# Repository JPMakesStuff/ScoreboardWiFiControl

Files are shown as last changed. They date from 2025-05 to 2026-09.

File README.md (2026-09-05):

# ScoreboardWiFiControl
Replacement for Varsity/All-Star/BSN/Sportable Baseball scoreboard controllers

Manufacturer's ancient and expensive remote was either a 5pin DIN connector that seemed to be RS-485 (but maybe not quite) or included the artaflex 2.4Ghz module (EOL 2018) which constantly disconnected; possibly because of a poorly designed heartbeat signal that can't ever be missed, or because it conflicted with every other 2.4Ghz WiFi network around. This remote drained batteries at an astounding rate; due to a design flaw where the power switch doesn't actually disconnect the battery.

Solution: Replace the manufacturer's control box with an [Arduino UNO R4 WiFi board](https://www.amazon.com/dp/B0C8V88Z9D), but keep the manufacturer dual output 35v/12v power supply that runs the LEDs.

Now anybody can use a **WiFi connected phone/tablet/laptop to control the scoreboard!**

Security should be accomplished by a dedicated wireless SSID just for the scoreboard(s) and for your coaches/announcers/trusted family member to connect.

Example webpage... (Make it an "app" icon using browser options menu, "Add to Home screen")<br/>
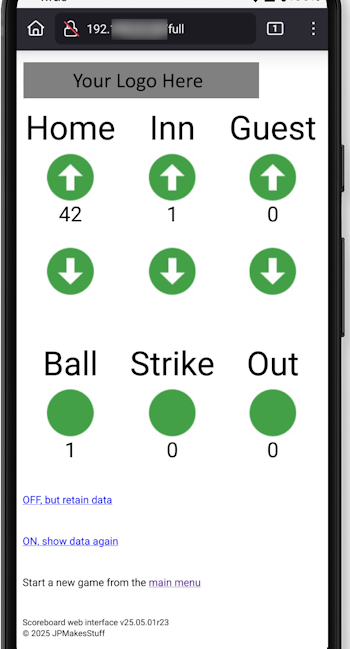
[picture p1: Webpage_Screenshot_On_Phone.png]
Webpage_Screenshot_On_Phone


## Software for Arduino

For the [3314](https://github.com/JPMakesStuff/ScoreboardWiFiControl/blob/main/3314.jpg) baseball scoreboard<br/>
...use the Arduino code "[ard_scoreboard](https://github.com/JPMakesStuff/ScoreboardWiFiControl/tree/main/ard_scoreboard)"

For the [3320](https://github.com/JPMakesStuff/ScoreboardWiFiControl/blob/main/3320.jpg) baseball scoreboard<br/>
...use the Arduino code "[ard_bigscoreboard](https://github.com/JPMakesStuff/ScoreboardWiFiControl/tree/main/ard_bigscoreboard)"

Graphics are a sprites file so there's only a single .png request (prevents upsetting Arduino's little web server as opposed to 10+ image requests)  If you want to insert your own logo and touch button graphics you could edit the [example .png graphic](https://github.com/JPMakesStuff/ScoreboardWiFiControl/blob/main/sprites_example.png), keeping the same placement and dimensions, then ask ChatGPT to create the arduino_images.h file from your .png file.

Your WiFi details need to be added in the arduino_secrets.h file.

To upload the sketch to your Arduino you need...
 - [Arduino IDE](https://www.arduino.cc/en/software/) (v2.3.8 as of today)
 - Install all the USB drivers when prompted
 - Tools > Board > Boards manager ... search "R4" ... Arduino UNO R4 Boards ... Install (v1.5.3 as of today)
 - Tools > Manage libraries ... search "graphics" ... ArduinoGraphics ... Install (v1.1.5 as of today)
 - Tools > Board > Arduino UNO R4 Boards > pick Arduino UNO R4
 - Tools > Port > pick COM # (the correct COM port number will be the one that shows up after plugging the Arduino into your computer)
 - Sketch > Upload

After applying power the Arduino's LED matrix briefly scrolls the last two octets of the IP address it got assigned. For example if your network DHCP server hands out 192.168.1.8 to the Arduino, the display would scroll 1.8
If this never happens then either your WiFi details are incorrect, out of range, you have some other network problem, or the Arduino is never fully booting.

## Hardware connections

The ribbon cable must be unplugged from the manufacturer's control box<br/>
(usually located behind the large hatch below or behind the inning digit)<br/>
Example pinout...<br/>
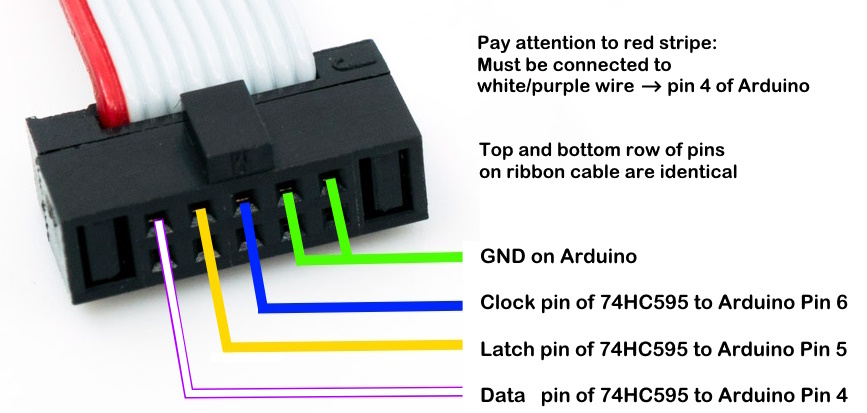
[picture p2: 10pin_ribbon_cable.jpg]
10pin connector


On the [cable I sell](https://jpelectron.etsy.com) pay attention to the colors plugged into the Arduino...<br/>
 - GND on Arduino is $\color{Green}{\textsf{Green}}$ wire</br>
 - Pin 6 on Arduino is $\color{Blue}{\textsf{Blue}}$ wire<br/>
 - Pin 5 on Arduino is $\color{Yellow}{\textsf{Yellow}}$ wire<br/>
 - Pin 4 on Arduino is White or $\color{Purple}{\textsf{Purple}}$ wire<br/>
...see the [picture here](https://github.com/JPMakesStuff/ScoreboardWiFiControl/blob/main/Example_Arduino_Connection.jpg) of Arduino connection</br>

Valid ways of connecting to the ribbon cable without butchering it are...<br/>
 - [cable I sell](https://jpelectron.etsy.com)
 - [Dual Rows 2.54mm 0.1" Pitch Shrouded IDC Male Header](https://www.amazon.com/dp/B00B3PI02G)
 - [Male IDC Socket 10 Pin 2x5 Pin 2.54mm Pitch](https://www.amazon.com/dp/B08T1YDG8M)

I spent days reverse engineering this, drop me a line if it helped you, or if you've adapted it to another model scoreboard!  If you'd like assistance in repair of your scoreboard or implementation of this new WiFi control method please contact me.  As of today I sell the [Arduino interface cable](https://www.etsy.com/listing/4490992543/arduino-to-baseball-scoreboard-control) on my Etsy shop and hope to offer full hardware conversion kits in the future if the demand is there.

## WiFi technical info

In my implementation we are using the following hardware...
 - TP-Link Omada firewall ER605v2 https://www.amazon.com/dp/B08QTXNWZ1<br/>
   ...also allows for content filtering to keep limited wireless bandwidth available for the GameChanger app
      (such as no YouTube, Hulu, Disney+ or adult sites)
 - TP-Link Omada wireless controller OC220 https://www.amazon.com/dp/B0FRW8GM11<br/>
   ...this is required to put the scoreboard mounted APs into mesh mode
 - TP-Link EAP610 Outdoor AP https://www.amazon.com/dp/B0B231J81C<br/>
   ...one goes on the concessions building, one goes on the scoreboard
 - Universal Wireless mount 2pk https://www.amazon.com/dp/B0BCNZFNTD<br/>
   ...makes it easy to mount the APs so they face each other
 - RasPi 4 model B with 4GB RAM https://www.amazon.com/dp/B07TD42S27<br/>
   ...this acts as a [Tailscale subnet router](https://tailscale.com/docs/features/subnet-routers) so I can control the scoreboards from anywhere, even when I'm home and not on the field WiFi

I intentionally decided to use an Arduino with WiFi as opposed to an Arduino with Ethernet; since each scoreboard has it's own AP mounted on it the signal is great and some level of lightning protection is achieved by not having a direct Ethernet connection to the AP.

As currently implemented both the Arduino and your end-users should connect to the same wireless SSID, the Arduino should be given a DHCP reservation (so the IP doesn't change) on the network, and optionally a DNS A record pointing to that IP for an easy to remember name.  Arduino code could be modified so the Arduino broadcasts it's own SSID (AP mode) but this is considerably less reliable in terms of WiFi channel saturation and end-user connection simplicity, so I strongly suggest against this. If the wireless doesn't actually provide Internet, users will have to pick "stay connected" on their device, some devices don't handle this well and won't continue to route Internet out the cellular connection resulting in loss of calls, text messages, or other app data.

## More technical info

Scoreboard digits are connected internally by a 10pin ribbon cable, of which only 4 pins are useful (doubled up for redundancy against broken lines, I guess?) This cable connects to a HC595 IC (8-Bit Shift Register), which turns "on" a channel of the ULN2803A (NPN Darlington Transistor Array) which allows 35v power to flow through a voltage regulator to 2 sets of 13 LEDs in series, which makes up a segment of the digit, or a dot.

On the [3314](https://github.com/JPMakesStuff/ScoreboardWiFiControl/blob/main/3314.jpg) baseball scoreboard this cable is routed like this...<br/>
Arduino --> Left home digit (10's) --> right home digit (1's) --> Inning --> Dot driver board --> Left guest digit --> Right guest digit<br/>
...remove the ribbon cable from control box found on the front side, hatch below the inning digit<br/>
See [3314 wiring diagram](https://github.com/JPMakesStuff/ScoreboardWiFiControl/blob/main/LED_repair_info/3314-Wiring-Diagram.png)

On the [3320](https://github.com/JPMakesStuff/ScoreboardWiFiControl/blob/main/3320.jpg) baseball scoreboard they routed this cable in what I suppose was efficient for saving on copper wire but full on silly for programming...<br/>
Arduino --> BallDigit, Inn1guest, Inn1home, Inn2home, Inn2guest, Inn3guest, Inn3home, Inn4home, Inn4guest, Inn5guest, Inn5home, Inn6home, Inn6guest, StrikeDigit, Inn7guest, Inn7home, Inn8home, Inn8guest, Inn9guest, Inn9home, LeftHomeDigit, RightHomeDigit, RightGuestDigit, LeftGuestDigit, OutDigit<br/>
...remove the ribbon cable from control box found on the front side, hatch above the 2nd inning guest score digit

Do NOT connect the ribbon cable to both your Arduino and the manufacture's control box at the same time, doing so will impede the signal to control any of the digits.

Arduino power should NOT be sourced from the custom 12v/35v power supply within the manufacture's control box as it doesn't seem to supply enough amperage for another load on the 12v rail, you will find that the Arduino randomly resets if many digits are 8 (all segments lit up)

I power the Arduino using a [5v 2amp USB power supply](https://www.amazon.com/dp/B07DCR29GN) feeding into either the USB-C port or the 5v pin on the Arduino.  Optionally you could also use a 7.5v or 9v power supply feeding into the barrel jack, realizing this is dropped down to 5v via Arduino's on-board voltage regulator.

120VAC can be obtained from the small hatch on the back of the scoreboard near the power entry point, or by using an [IEC splitter](https://www.amazon.com/dp/B0BGPXDYSM) before it goes into the manufacture's control box.

Note on the manufacture's power supply located inside the control box...<br/>
MeanWell PD85-SP with dual output 12VDC 0.25A + 35VDC 2.3A (which I can't find anywhere today, perhaps was custom built just for Varsity)<br/>
Someday this will die and I expect having to source a more common 36v supply and using the internal trim pot found on most MeanWell supply's to make it output 35v, having a separate 12v power supply, then connecting both GNDs together.<br/>
 - Red wire is 35v rail - used to power the LED segments via several voltage regulators, one for each segment of the 7-segment digit<br/>
 - Brown wire is 12v rail - used to power a single voltage regulator on each digit which drops to 5v to power the HC595 and ULN2803A chips<br/>
 - Black wire is GND<br/>

In my case the scoreboards were all outdoors and all seemed to be getting wet inside, plus the fact that it's a big metal box means putting the Arduino inside the scoreboard isn't the best for WiFi connectivity, so I elected to move the power supply and control circuitry to a [weatherproof box](https://www.amazon.com/dp/B0BFPXDN8M) and split the 120VAC using [this terminal block](https://www.amazon.com/dp/B0DNJRQP32).  Each scoreboard has a wireless AP in a mesh configuration that connects them all back to the source of the WiFi at the concessions building.

See [example of my new control box](https://github.com/JPMakesStuff/ScoreboardWiFiControl/blob/main/Example_control_box.jpg)

## LED digit or dot testing aid

To test individual digit boards, or the "vane driver" board for (ball/strike/out) dots<br/>
Arduino --> 10pin ribbon cable --> only one digit at a time, not the entire scoreboard!<br/>
 - no other digits should be daisy-chained via additional ribbon cables connected to "output"<br/>
 - it's OK to keep the 3pin power cable connected to all, unless your trying to isolate a damaged/corroded/shorted digit or dot<br/>
 - **you MUST connect all GND together: the Arduino GND to the ribbon cable GND is then connected to the power supply GND via the digit**<br/>
 - use the Arduino code "[LED_tester](https://github.com/JPMakesStuff/ScoreboardWiFiControl/tree/main/LED_tester)"<br/>
 - modify the SSID section near the top to match your WiFi on the field, or your home WiFi, or your phone's hotspot when testing anywhere

See [example of test page](https://github.com/JPMakesStuff/ScoreboardWiFiControl/blob/main/Webpage_Screenshot_LED_tester.png)

## LED repair info

Digit<br/>
PCB - 1600129<br/>
PCA - 1500129<br/>
REV C<br/>

Dots<br/>
PCB - 1600131<br/>
PCA - 1500131<br/>
REV A<br/>

35v in → LM317 + 30 Ω → ~42 mA constant current → two parallel strings of 13 × 1.8v LEDs (voltage of drop ~23.4v) → ~20–21 mA per LED

LED size = T-1 3/4 5mm = DigiKey part 350-5218765F-ND, Mfg part 5218765F by Dialight

https://varsityscoreboards.com/scoreboard-parts/led-dots/replacement-2-inch-outdoor-dot/

https://varsityscoreboards.com/uncategorized/vane-dot-driver-board-1500055

https://varsityscoreboards.com/uncategorized/outdoor-15-led-digit-panel-1501015-12

See [LED repair info](https://github.com/JPMakesStuff/ScoreboardWiFiControl/blob/main/LED_repair_info)

## Notes for cost comparison

~$263 for my control box (including conformal coating the PCBs, caulk, weatherproof box, screws, Arduino, 5v power supply, and wireless AP)

https://scoreboard-parts.com/1006647-Semtech-Sportable-Varsity-Scoreboard-Driver-101MOD2.html
$975 | SKU# 1006647-Semtech

https://scoreboard-parts.com/1006649-SEMTECH-Sportable-Varsity-Wireless-Controller.html
$950 | SKU# 1006649-SEMTECH

https://scoreboard-parts.com/101MOD2-Sportable-Varsity-Scoreboard-Driver.html
$1,562.95 | SKU# 101MOD2

https://scoreboard-parts.com/1001LCDW-Sportable-Varsity-Wireless-Controller.HTML
$1,824.95 | SKU# 1001LCDW

...I'm not paying that for something that disconnects and resets the score 95% of the time.

[How it's made YouTube video](https://www.youtube.com/watch?v=2Ui810LpJfk) showing scoreboard assembly process

[Outdoor installation video](https://www.youtube.com/watch?v=sqrrQPMJL8o) by the same company

[End of Line]

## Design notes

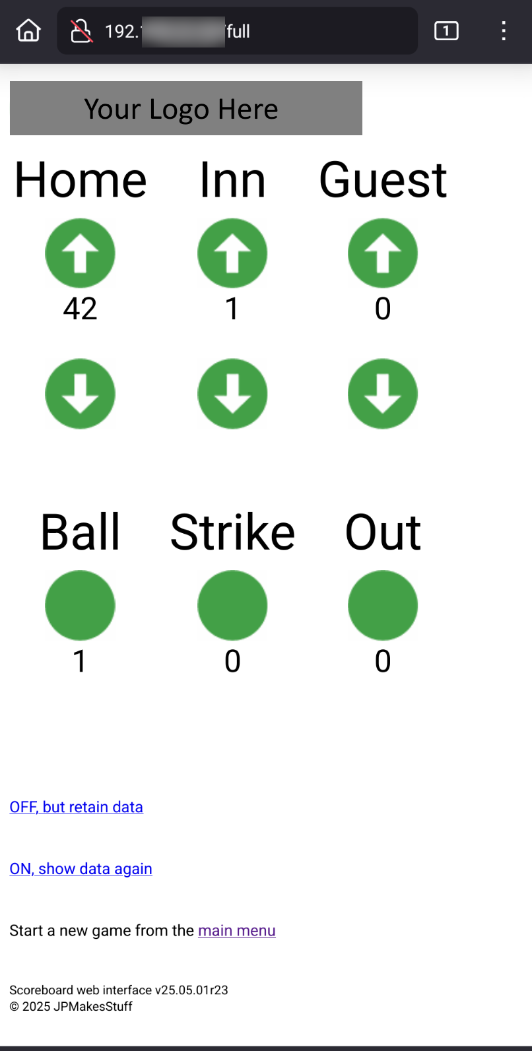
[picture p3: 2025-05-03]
Webpage_Screenshot.png

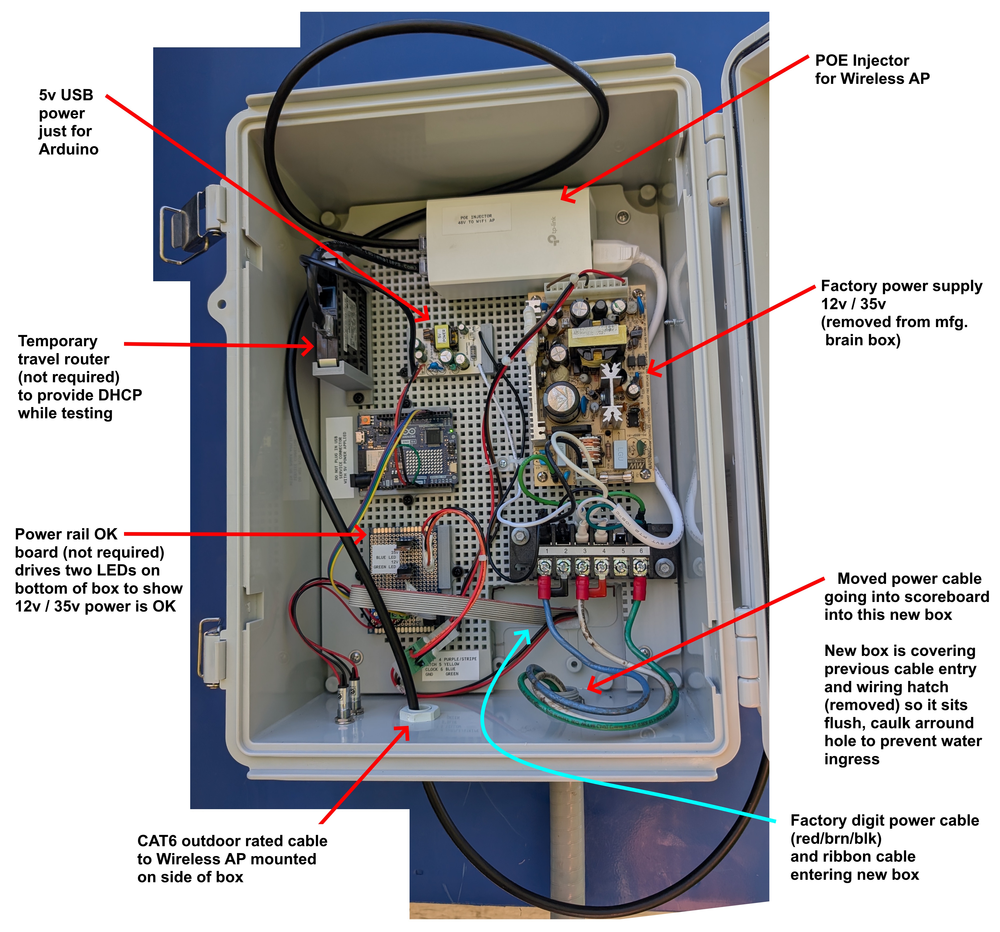
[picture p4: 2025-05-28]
Example_control_box.jpg

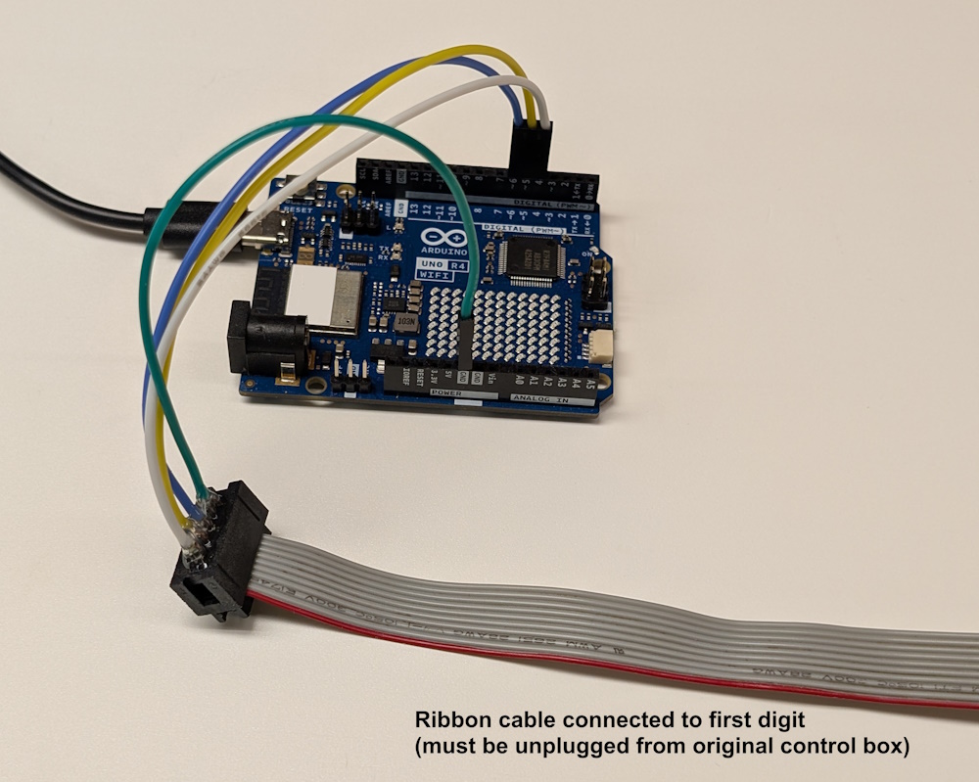
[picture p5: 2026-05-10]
Example_Arduino_Connection.jpg

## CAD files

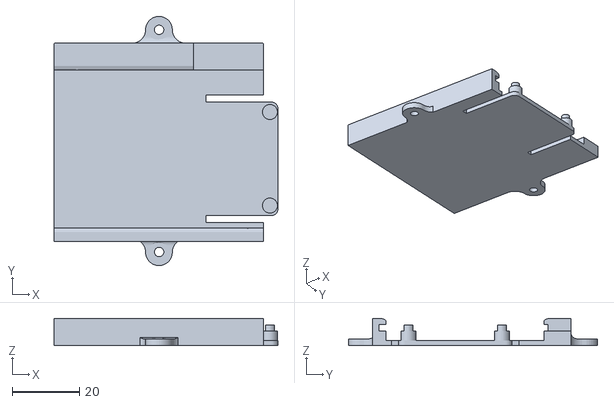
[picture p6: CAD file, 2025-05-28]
3D_print_files/Baseball SB Connections vReg PCB mount.stl
66.8 x 74.3 x 8.10

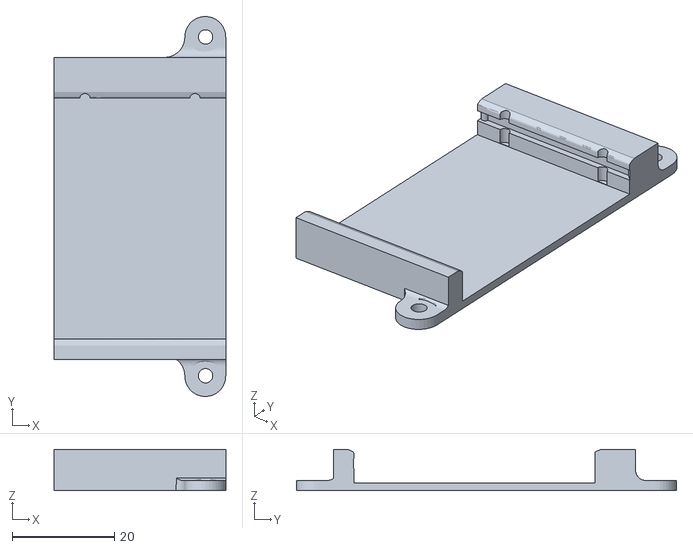
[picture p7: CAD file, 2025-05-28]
3D_print_files/Baseball SB 5v 2a PS mount.stl
33.6 x 74.3 x 8.10

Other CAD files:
3D_print_files/Baseball SB Arduino mount.stl

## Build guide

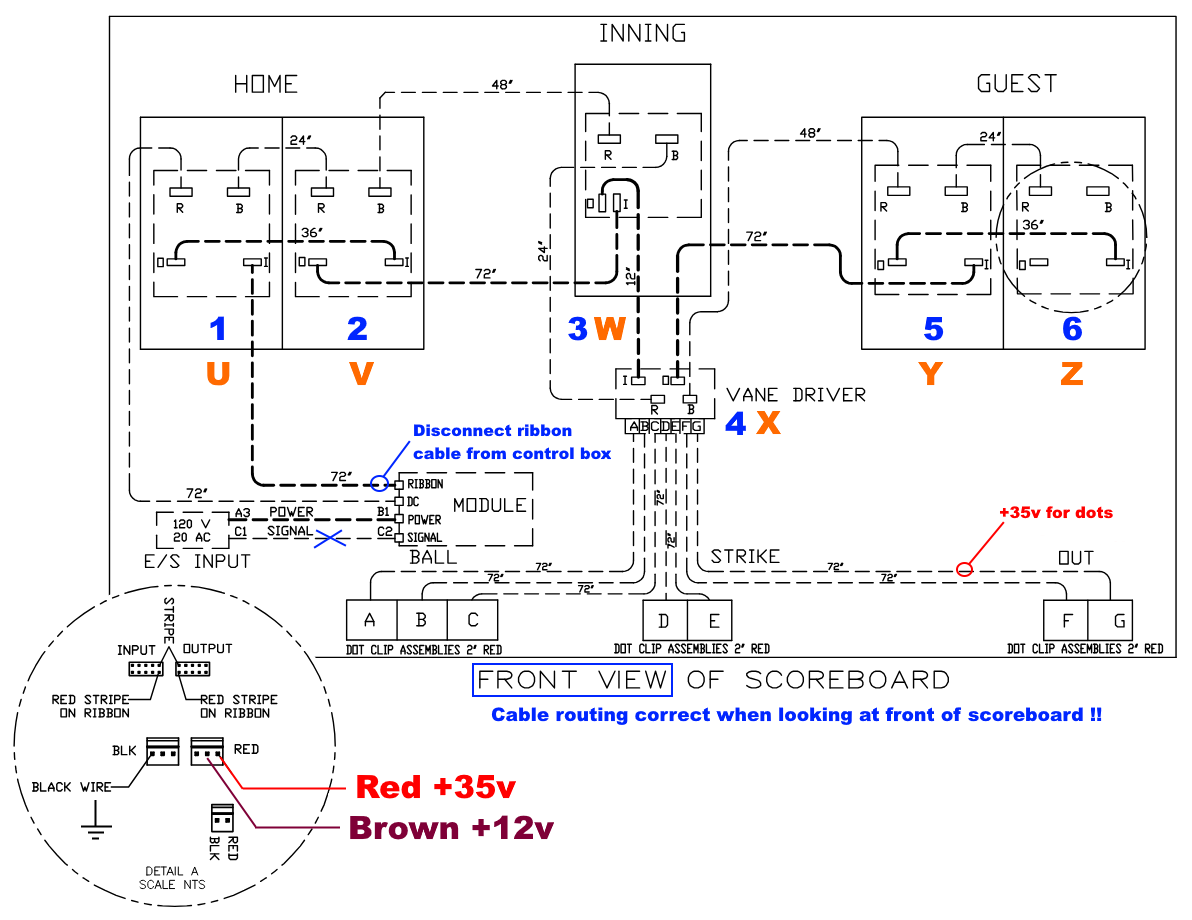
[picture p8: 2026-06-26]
LED_repair_info/3314-Wiring-Diagram.png

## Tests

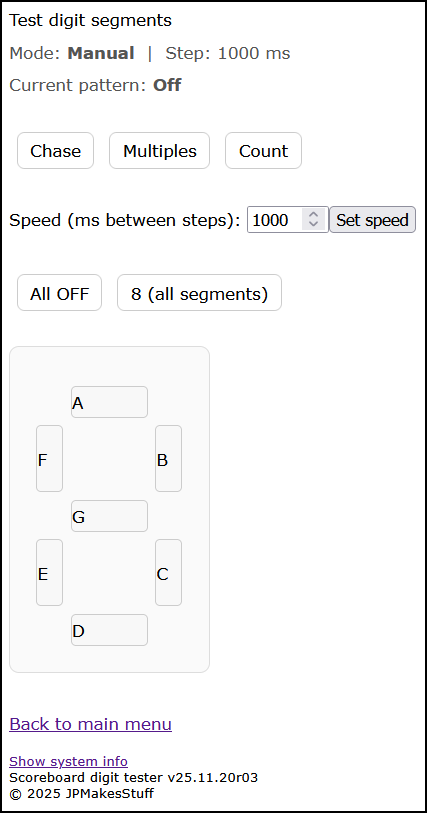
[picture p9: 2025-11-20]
Webpage_Screenshot_LED_tester.png

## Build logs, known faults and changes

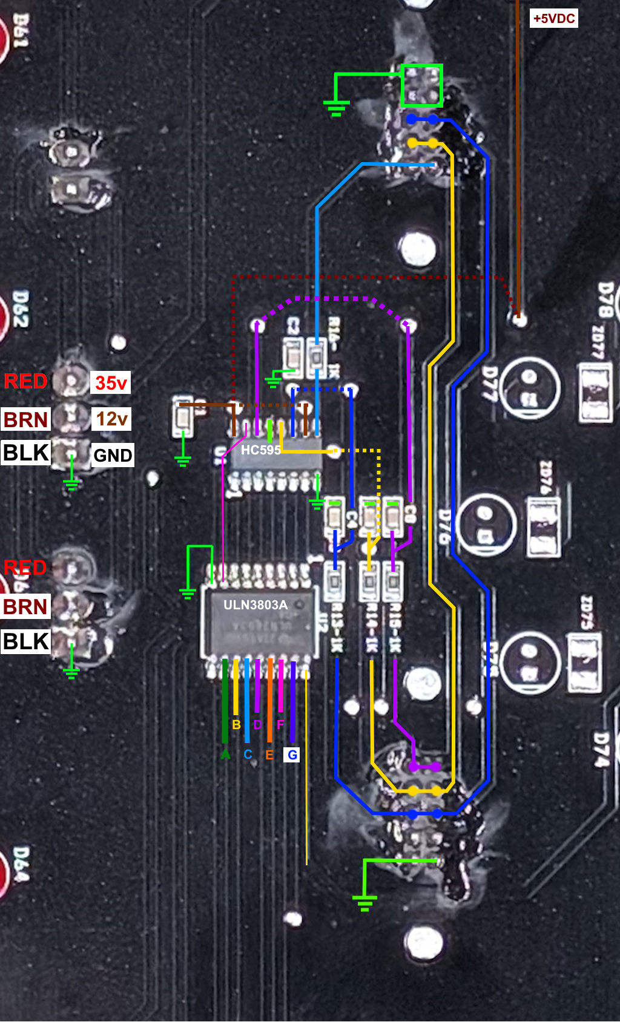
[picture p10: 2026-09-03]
LED_repair_info/digit_circuit_diagram_ICs.png

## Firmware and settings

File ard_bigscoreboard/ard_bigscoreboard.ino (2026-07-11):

#include "WiFiS3.h"
#include "arduino_secrets.h"

#include "arduino_images.h"

#include "ArduinoGraphics.h"
#include "Arduino_LED_Matrix.h"
ArduinoLEDMatrix matrix;

char ssid[] = SECRET_SSID; // do not update SSID and PASS here, put it in arduino_secrets.h
char pass[] = SECRET_PASS;
int keyIndex = 0;

// store the software version
char swver[] = "26.07.10r08";

// declair pins
int dataPin = 4;	// Data pin of 74HC595 is connected to Digital pin 4 (purple wire to digit ribbon cable)
int latchPin = 5;	// Latch pin of 74HC595 is connected to Digital pin 5 (yellow wire to digit ribbon cable)
int clockPin = 6;	// Clock pin of 74HC595 is connected to Digital pin 6 (blue wire to digit ribbon cable)
    // dont forget GND connection (green wire to digit ribbon cable)

// Digit index mapping based on wiring order from Arduino to shift registers
#define DIGIT_BALL         0
#define DIGIT_INN1_GUEST   1
#define DIGIT_INN1_HOME    2
#define DIGIT_INN2_HOME    3
#define DIGIT_INN2_GUEST   4
#define DIGIT_INN3_GUEST   5
#define DIGIT_INN3_HOME    6
#define DIGIT_INN4_HOME    7
#define DIGIT_INN4_GUEST   8
#define DIGIT_INN5_GUEST   9
#define DIGIT_INN5_HOME    10
#define DIGIT_INN6_HOME    11
#define DIGIT_INN6_GUEST   12
#define DIGIT_STRIKE       13
#define DIGIT_INN7_GUEST   14
#define DIGIT_INN7_HOME    15
#define DIGIT_INN8_HOME    16
#define DIGIT_INN8_GUEST   17
#define DIGIT_INN9_GUEST   18
#define DIGIT_INN9_HOME    19
#define DIGIT_HOME_TENS    20
#define DIGIT_HOME_ONES    21
#define DIGIT_GUEST_ONES   22
#define DIGIT_GUEST_TENS   23
#define DIGIT_OUT          24

int digits[25]; // Holds values 0–9 or 10 (for blank/off)

int digits_backup[25];  // Holds previous state for /restore

int guestInningScores[9] = {0};
int homeInningScores[9] = {0};

// --- Helper functions ---
int guestInningDigitIndex(int inning) {
  switch (inning) {
    case 1: return DIGIT_INN1_GUEST;
    case 2: return DIGIT_INN2_GUEST;
    case 3: return DIGIT_INN3_GUEST;
    case 4: return DIGIT_INN4_GUEST;
    case 5: return DIGIT_INN5_GUEST;
    case 6: return DIGIT_INN6_GUEST;
    case 7: return DIGIT_INN7_GUEST;
    case 8: return DIGIT_INN8_GUEST;
    case 9: return DIGIT_INN9_GUEST;
  }
  return -1;
}

int homeInningDigitIndex(int inning) {
  switch (inning) {
    case 1: return DIGIT_INN1_HOME;
    case 2: return DIGIT_INN2_HOME;
    case 3: return DIGIT_INN3_HOME;
    case 4: return DIGIT_INN4_HOME;
    case 5: return DIGIT_INN5_HOME;
    case 6: return DIGIT_INN6_HOME;
    case 7: return DIGIT_INN7_HOME;
    case 8: return DIGIT_INN8_HOME;
    case 9: return DIGIT_INN9_HOME;
  }
  return -1;
}

int lastGuestTotal = 0;
int lastHomeTotal  = 0;
int currentInning = 1;

// store values globally for actual score
int ballCount = 0;    // 0–3 (for dots A–C)
int strikeCount = 0;  // 0–2 (for dots D–E)
int outCount = 0;     // 0–2 (for dots F–G)

// to control each 7-segment digit
const byte digitToSegmentMap[11] = {
  B00111111, // Zero
  B00000110, // One
  B01011011, // Two
  B01001111, // Three
  B01100110, // Four
  B01101101, // Five
  B01111101, // Six
  B00000111, // Seven
  B01111111, // Eight
  B01101111, // Nine
  B00000000, // 10 = ALL SEGMENTS (or DOTs) OFF
};
// x        segment DP (not used so leave 0 for off)
//  x       segment position G on (also Out 2)
//   x      segment position F on (also Out 1)
//    x     segment position E on (also Strike 2)
//     x    segment position D on (also Strike 1)
//      x   segment position C on (also Ball 3)
//       x  segment position B on (also Ball 2)
//        x segment position A on (also Ball 1)

byte mac[6];  // the MAC address of WiFi module

int status = WL_IDLE_STATUS;
WiFiServer server(80);


void setup() 
{

  // set all the pins of 74HC595 as OUTPUT
  pinMode(latchPin, OUTPUT);
  pinMode(dataPin, OUTPUT);  
  pinMode(clockPin, OUTPUT);

  //Serial.begin(9600);      // initialize serial communication

  // check for the WiFi module:
  if (WiFi.status() == WL_NO_MODULE) {
    //Serial.println("Communication with WiFi module failed!");
    // don't continue
    while (true);
  }

  // check for the firmware upgrade:
  String fv = WiFi.firmwareVersion();
  if (fv < WIFI_FIRMWARE_LATEST_VERSION) {
    //Serial.println("Please upgrade the firmware");
  }

  // attempt to connect to WiFi network:
  while (status != WL_CONNECTED) {
    //Serial.print("Attempting to connect to Network named: ");
    //Serial.println(ssid);  // print the network name (SSID);
    // Connect to WPA/WPA2 network. Change this line if using open or WEP network:
    status = WiFi.begin(ssid, pass);
    // wait 15 seconds for connection:
    delay(15000);
  }

  server.begin();     // start the web server on port 80

  IPAddress localIP = WiFi.localIP();

  // displaying the IP below let's the end-user know we're done booting

  // reset all digits to off just incase
  for (int i = 0; i < 25; i++) {
    digits[i] = 10;
  }
  digit_update();

  //this scrolls the 3rd and 4th octets of the IP on the Arduino UNO R4 WiFi's built-in LED matrix
  String ipStr = "." + String(localIP[2]) + "." + String(localIP[3]);  // show only 3rd and 4th octets (index 2 and 3)
  matrix.begin();
  matrix.beginDraw();
  matrix.stroke(0xFFFFFFFF);
  matrix.textScrollSpeed(50);
  matrix.textFont(Font_4x6);
  matrix.beginText(0, 1, 0xFFFFFF);
  matrix.println(ipStr);
  matrix.endText(SCROLL_LEFT);
  matrix.endDraw();

  // this displays the 3rd and 4th octets of the IP on the scoreboards per-inning home score digits
  String part3Str = String(localIP[2]);
  String part4Str = String(localIP[3]);

  // since there are no decimals on scoreboard digits a blank digit will represent the decimal between IP octets
  int displayDigits[7];  // up to 3 digits + blank digit + up to 3 digits
  int idx = 0;

  // Add digits for part 3 (octet 3)
  for (int i = 0; i < part3Str.length() && idx < 3; i++) {
    displayDigits[idx++] = part3Str.charAt(i) - '0';
  }

  // Add blank space separator
  displayDigits[idx++] = 10;  // blank

  // Add digits for part 4 (octet 4)
  for (int i = 0; i < part4Str.length() && idx < 6; i++) {
    displayDigits[idx++] = part4Str.charAt(i) - '0';
  }

  // Fill any unused positions with blank
  while (idx < 7) {
    displayDigits[idx++] = 10;
  }

  // Assign to per-inning home digits
  int digitPositions[7] = {2, 4, 6, 8, 10, 12, 14};
  for (int i = 0; i < 7; i++) {
    digits[digitPositions[i]] = displayDigits[i];
  }

  digit_update();
  delay(4000);  // Show for 4 seconds

  // start a new game

  // Reset inning scores and totals
  for (int i = 0; i < 9; i++) {
    guestInningScores[i] = 0;
    homeInningScores[i] = 0;
  }

  ballCount = 0;
  strikeCount = 0;
  outCount = 0;
  lastGuestTotal = 0;
  lastHomeTotal = 0;
  currentInning = 1;

  // Set B/S/O to 0
  digits[DIGIT_BALL] = 10;    //set 10 means digit is off
  digits[DIGIT_STRIKE] = 10;  //set 10 means digit is off
  digits[DIGIT_OUT] = 10;     //set 10 means digit is off

  // Show 0 on inning 1 digits to indicate it's the start of inning 1
  updateInningDigit(DIGIT_INN1_GUEST, 0, 1);
  updateInningDigit(DIGIT_INN1_HOME, 0, 1);

  // Show 0 for Guest and Home total scores
  digits[DIGIT_GUEST_TENS] = 10; //set 10 means digit is off
  digits[DIGIT_GUEST_ONES] = 0;
  digits[DIGIT_HOME_TENS] = 10;  //set 10 means digit is off
  digits[DIGIT_HOME_ONES] = 0;

digit_update();

}


void loop() 
{

WiFiClient client = server.available();   // listen for incoming clients

  if (client) {                           // if you get a client
    String request = "";
      while (client.available()) {
        String line = client.readStringUntil('\n');
        if (line.length() == 1 && line[0] == '\r') break;
        if (request == "") request = line;
      }

        // HTTP headers always start with a response code
        if (request.indexOf("GET /favicon.ico") >= 0) {
          client.println("HTTP/1.1 404 Not Found");   // here is the error response code
          client.println("Content-Type: text/plain");
          client.println("Connection: close");
          client.println();
          client.println("404 Not Found");
          client.stop();  // close connection
          return;         // stop processing this loop()
        }
        else {
          client.println("HTTP/1.1 200 OK");          // here is a normal response code
        }

        // image first since header is different
        // using image sprite to save memory
        if (request.indexOf("GET /sprites.png") >= 0) {
          client.println("Content-Type: image/png");
          client.println("Content-Length: " + String(sprites_png_len));
          client.println("Cache-Control: max-age=86400");  // browser cache for 1 day
          client.println("Connection: close");
          client.println();
          client.write(sprites_png, sprites_png_len);
        }
        // otherwise its the normal text/html content below
        else {
          client.println("Content-type:text/html");
          client.println("Connection: close");
          client.println();
        }

        // otherwise the content of the HTTP response follows the header

        // check if the client request was "GET /placeholder" used in quick remote and main page iframes
        if (request.indexOf("GET /placeholder") >= 0) {
        }

        // HOME SCORE UP - request may come from either remote page
        else if (request.indexOf("GET /hup") >= 0) {
          int total = lastHomeTotal + 1;
          if (total <= 99) {
            int idx = currentInning - 1;
            homeInningScores[idx] += 1;
            lastHomeTotal = total;

            // Update digits
            digits[DIGIT_HOME_TENS] = total / 10;
            digits[DIGIT_HOME_ONES] = total % 10;

            switch (currentInning) {
              case 1: updateInningDigit(DIGIT_INN1_HOME, homeInningScores[idx], 1); break;
              case 2: updateInningDigit(DIGIT_INN2_HOME, homeInningScores[idx], 2); break;
              case 3: updateInningDigit(DIGIT_INN3_HOME, homeInningScores[idx], 3); break;
              case 4: updateInningDigit(DIGIT_INN4_HOME, homeInningScores[idx], 4); break;
              case 5: updateInningDigit(DIGIT_INN5_HOME, homeInningScores[idx], 5); break;
              case 6: updateInningDigit(DIGIT_INN6_HOME, homeInningScores[idx], 6); break;
              case 7: updateInningDigit(DIGIT_INN7_HOME, homeInningScores[idx], 7); break;
              case 8: updateInningDigit(DIGIT_INN8_HOME, homeInningScores[idx], 8); break;
              case 9: updateInningDigit(DIGIT_INN9_HOME, homeInningScores[idx], 9); break;
            }

            digit_update();
            if (request.indexOf("show=yes") >= 0) {
              client.print("<html><head>");
              client.print("</head><body>");
              client.print("<font face=\"Verdana\" style=\"font-size: 20pt\">");
              client.print("<center>");
              client.print(lastHomeTotal);
            }
          }
        }

        // HOME SCORE DOWN - request may come from either remote page
        else if (request.indexOf("GET /hdn") >= 0) {
          int total = lastHomeTotal - 1;
          if (total >= 0) {
            int idx = currentInning - 1;
            homeInningScores[idx] -= 1;
            lastHomeTotal = total;

            digits[DIGIT_HOME_TENS] = total / 10;
            digits[DIGIT_HOME_ONES] = total % 10;

            switch (currentInning) {
              case 1: updateInningDigit(DIGIT_INN1_HOME, homeInningScores[idx], 1); break;
              case 2: updateInningDigit(DIGIT_INN2_HOME, homeInningScores[idx], 2); break;
              case 3: updateInningDigit(DIGIT_INN3_HOME, homeInningScores[idx], 3); break;
              case 4: updateInningDigit(DIGIT_INN4_HOME, homeInningScores[idx], 4); break;
              case 5: updateInningDigit(DIGIT_INN5_HOME, homeInningScores[idx], 5); break;
              case 6: updateInningDigit(DIGIT_INN6_HOME, homeInningScores[idx], 6); break;
              case 7: updateInningDigit(DIGIT_INN7_HOME, homeInningScores[idx], 7); break;
              case 8: updateInningDigit(DIGIT_INN8_HOME, homeInningScores[idx], 8); break;
              case 9: updateInningDigit(DIGIT_INN9_HOME, homeInningScores[idx], 9); break;
            }

            digit_update();
            if (request.indexOf("show=yes") >= 0) {
              client.print("<html><head>");
              client.print("</head><body>");
              client.print("<font face=\"Verdana\" style=\"font-size: 20pt\">");
              client.print("<center>");
              client.print(lastHomeTotal);
            }
          }
        }

        // INNING UP - request may come from either remote page
        else if (request.indexOf("GET /iup") >= 0) {
          // Advance to next inning, wrap from 9 → 1
          currentInning = (currentInning == 9) ? 1 : currentInning + 1;

          int idx = currentInning - 1;

          // If not yet initialized, make sure the inning score arrays are zeroed
          guestInningScores[idx] = 0;
          homeInningScores[idx] = 0;

          // Show a 0 on the digit displays for new inning
          switch (currentInning) {
            case 1:
              updateInningDigit(DIGIT_INN1_GUEST, 0, 1);
              updateInningDigit(DIGIT_INN1_HOME,  0, 1);
              break;
            case 2:
              updateInningDigit(DIGIT_INN2_GUEST, 0, 2);
              updateInningDigit(DIGIT_INN2_HOME,  0, 2);
              break;
            case 3:
              updateInningDigit(DIGIT_INN3_GUEST, 0, 3);
              updateInningDigit(DIGIT_INN3_HOME,  0, 3);
              break;
            case 4:
              updateInningDigit(DIGIT_INN4_GUEST, 0, 4);
              updateInningDigit(DIGIT_INN4_HOME,  0, 4);
              break;
            case 5:
              updateInningDigit(DIGIT_INN5_GUEST, 0, 5);
              updateInningDigit(DIGIT_INN5_HOME,  0, 5);
              break;
            case 6:
              updateInningDigit(DIGIT_INN6_GUEST, 0, 6);
              updateInningDigit(DIGIT_INN6_HOME,  0, 6);
              break;
            case 7:
              updateInningDigit(DIGIT_INN7_GUEST, 0, 7);
              updateInningDigit(DIGIT_INN7_HOME,  0, 7);
              break;
            case 8:
              updateInningDigit(DIGIT_INN8_GUEST, 0, 8);
              updateInningDigit(DIGIT_INN8_HOME,  0, 8);
              break;
            case 9:
              updateInningDigit(DIGIT_INN9_GUEST, 0, 9);
              updateInningDigit(DIGIT_INN9_HOME,  0, 9);
              break;
          }

          // Reset B/S/O logic and display
          ballCount = 0;
          strikeCount = 0;
          outCount = 0;
          digits[DIGIT_BALL]   = 10;
          digits[DIGIT_STRIKE] = 10;
          digits[DIGIT_OUT]    = 10;

          digit_update();

          if (request.indexOf("show=yes") >= 0) {
            client.print("<html><head>");
            // must refresh the whole page otherwise B/S/O could be showing old data
            client.print("<meta http-equiv=\"refresh\" content=\"1; url=/full\">");
            client.print("</head><body>");
            client.print("<font face=\"Verdana\" style=\"font-size: 20pt\">");
            client.print("<center>");
            client.print("One moment...");
          }
        }


        // INNING DOWN - request may come from either remote page
        else if (request.indexOf("GET /idn") >= 0) {
          int eraseInning = currentInning;
          int eraseIdx = eraseInning - 1;

          // Subtract scores from totals
          lastGuestTotal -= guestInningScores[eraseIdx];
          lastHomeTotal  -= homeInningScores[eraseIdx];

          // Zero out the inning scores
          guestInningScores[eraseIdx] = 0;
          homeInningScores[eraseIdx] = 0;

          // Blank the digit display for the inning being cleared
          switch (eraseInning) {
            case 1: digits[DIGIT_INN1_GUEST] = 10; digits[DIGIT_INN1_HOME] = 10; break;
            case 2: digits[DIGIT_INN2_GUEST] = 10; digits[DIGIT_INN2_HOME] = 10; break;
            case 3: digits[DIGIT_INN3_GUEST] = 10; digits[DIGIT_INN3_HOME] = 10; break;
            case 4: digits[DIGIT_INN4_GUEST] = 10; digits[DIGIT_INN4_HOME] = 10; break;
            case 5: digits[DIGIT_INN5_GUEST] = 10; digits[DIGIT_INN5_HOME] = 10; break;
            case 6: digits[DIGIT_INN6_GUEST] = 10; digits[DIGIT_INN6_HOME] = 10; break;
            case 7: digits[DIGIT_INN7_GUEST] = 10; digits[DIGIT_INN7_HOME] = 10; break;
            case 8: digits[DIGIT_INN8_GUEST] = 10; digits[DIGIT_INN8_HOME] = 10; break;
            case 9: digits[DIGIT_INN9_GUEST] = 10; digits[DIGIT_INN9_HOME] = 10; break;
          }

          // Update the total score display
          digits[DIGIT_GUEST_TENS] = lastGuestTotal / 10;
          digits[DIGIT_GUEST_ONES] = lastGuestTotal % 10;
          digits[DIGIT_HOME_TENS]  = lastHomeTotal  / 10;
          digits[DIGIT_HOME_ONES]  = lastHomeTotal  % 10;

          // Go back one inning
          currentInning = (currentInning == 1) ? 9 : currentInning - 1;
          int idx = currentInning - 1;

          // Re-display inning digits for the new current inning
          switch (currentInning) {
            case 1:
              updateInningDigit(DIGIT_INN1_GUEST, guestInningScores[idx], 1);
              updateInningDigit(DIGIT_INN1_HOME, homeInningScores[idx], 1);
              break;
            case 2:
              updateInningDigit(DIGIT_INN2_GUEST, guestInningScores[idx], 2);
              updateInningDigit(DIGIT_INN2_HOME, homeInningScores[idx], 2);
              break;
            case 3:
              updateInningDigit(DIGIT_INN3_GUEST, guestInningScores[idx], 3);
              updateInningDigit(DIGIT_INN3_HOME, homeInningScores[idx], 3);
              break;
            case 4:
              updateInningDigit(DIGIT_INN4_GUEST, guestInningScores[idx], 4);
              updateInningDigit(DIGIT_INN4_HOME, homeInningScores[idx], 4);
              break;
            case 5:
              updateInningDigit(DIGIT_INN5_GUEST, guestInningScores[idx], 5);
              updateInningDigit(DIGIT_INN5_HOME, homeInningScores[idx], 5);
              break;
            case 6:
              updateInningDigit(DIGIT_INN6_GUEST, guestInningScores[idx], 6);
              updateInningDigit(DIGIT_INN6_HOME, homeInningScores[idx], 6);
              break;
            case 7:
              updateInningDigit(DIGIT_INN7_GUEST, guestInningScores[idx], 7);
              updateInningDigit(DIGIT_INN7_HOME, homeInningScores[idx], 7);
              break;
            case 8:
              updateInningDigit(DIGIT_INN8_GUEST, guestInningScores[idx], 8);
              updateInningDigit(DIGIT_INN8_HOME, homeInningScores[idx], 8);
              break;
            case 9:
              updateInningDigit(DIGIT_INN9_GUEST, guestInningScores[idx], 9);
              updateInningDigit(DIGIT_INN9_HOME, homeInningScores[idx], 9);
              break;
          }

          // Clear B/S/O as part of going back an inning
          ballCount = 0;
          strikeCount = 0;
          outCount = 0;
          digits[DIGIT_BALL] = 10;
          digits[DIGIT_STRIKE] = 10;
          digits[DIGIT_OUT] = 10;

          digit_update();

          if (request.indexOf("show=yes") >= 0) {
            client.print("<html><head>");
            // must refresh the whole page otherwise B/S/O could be showing old data
            client.print("<meta http-equiv=\"refresh\" content=\"1; url=/full\">");
            client.print("</head><body>");
            client.print("<font face=\"Verdana\" style=\"font-size: 20pt\">");
            client.print("<center>");
            client.print("One moment...");
          }
        }


        // GUEST SCORE UP - request may come from either remote page
        else if (request.indexOf("GET /gup") >= 0) {
          int total = lastGuestTotal + 1;
          if (total <= 99) {
            int idx = currentInning - 1;
            guestInningScores[idx] += 1;
            lastGuestTotal = total;

            // Update digits
            digits[DIGIT_GUEST_TENS] = total / 10;
            digits[DIGIT_GUEST_ONES] = total % 10;

            switch (currentInning) {
              case 1: updateInningDigit(DIGIT_INN1_GUEST, guestInningScores[idx], 1); break;
              case 2: updateInningDigit(DIGIT_INN2_GUEST, guestInningScores[idx], 2); break;
              case 3: updateInningDigit(DIGIT_INN3_GUEST, guestInningScores[idx], 3); break;
              case 4: updateInningDigit(DIGIT_INN4_GUEST, guestInningScores[idx], 4); break;
              case 5: updateInningDigit(DIGIT_INN5_GUEST, guestInningScores[idx], 5); break;
              case 6: updateInningDigit(DIGIT_INN6_GUEST, guestInningScores[idx], 6); break;
              case 7: updateInningDigit(DIGIT_INN7_GUEST, guestInningScores[idx], 7); break;
              case 8: updateInningDigit(DIGIT_INN8_GUEST, guestInningScores[idx], 8); break;
              case 9: updateInningDigit(DIGIT_INN9_GUEST, guestInningScores[idx], 9); break;
            }

            digit_update();
            if (request.indexOf("show=yes") >= 0) {
              client.print("<html><head>");
              client.print("</head><body>");
              client.print("<font face=\"Verdana\" style=\"font-size: 20pt\">");
              client.print("<center>");
              client.print(lastGuestTotal);
            }
          }
        }

        // GUEST SCORE DOWN - request may come from either remote page
        else if (request.indexOf("GET /gdn") >= 0) {
          int total = lastGuestTotal - 1;
          if (total >= 0) {
            int idx = currentInning - 1;
            guestInningScores[idx] -= 1;
            lastGuestTotal = total;

            digits[DIGIT_GUEST_TENS] = total / 10;
            digits[DIGIT_GUEST_ONES] = total % 10;
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

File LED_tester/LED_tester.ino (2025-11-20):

#include "WiFiS3.h"

#include "ArduinoGraphics.h"
#include "Arduino_LED_Matrix.h"
ArduinoLEDMatrix matrix;

// Fill these in to match your scoreboard WiFi
// ---------- PRIMARY WIFI ----------
char ssid1[] = "[PUT_YOUR_SSID_HERE]";
char pass1[] = "[PUT_YOUR_PASSWORD_HERE]";

// Fill these in to match your phone hotspot or home network for testing
// ---------- FALLBACK WIFI ----------
char ssid2[] = "AlternateWiFi";
char pass2[] = "AlternatePass";

// which WiFi did we end up on 1 = primary, 2 = fallback
int activeNet = 0;

// store the software version
char swver[] = "25.11.20r03";

// declair pins
int dataPin = 4;	// Data pin of 74HC595 is connected to Digital pin 4 (purple wire to digit ribbon cable)
int latchPin = 5;	// Latch pin of 74HC595 is connected to Digital pin 5 (yellow wire to digit ribbon cable)
int clockPin = 6;	// Clock pin of 74HC595 is connected to Digital pin 6 (blue wire to digit ribbon cable)
    // dont forget GND connection (green wire to digit ribbon cable)

// store value for each dot, but initially set to off = 0 (otherwise send 1 = on)
int dotA = 0;
int dotB = 0;
int dotC = 0;
int dotD = 0;
int dotE = 0;
int dotF = 0;
int dotG = 0;

// to control each 7-segment digit
byte num[] = {
  B00111111, // Zero
  B00000110, // One
  B01011011, // Two
  B01001111, // Three
  B01100110, // Four
  B01101101, // Five
  B01111101, // Six
  B00000111, // Seven
  B01111111, // Eight
  B01101111, // Nine
  B00000000, // 10 = ALL SEGMENTS (or DOTs) OFF
  B00000001, // 11 = segment A only
  B00000010, // 12 = segment B only
  B00000100, // 13 = segment C only
  B00001000, // 14 = segment D only
  B00010000, // 15 = segment E only
  B00100000, // 16 = segment F only
  B01000000, // 17 = segment G only
};
// x        segment DP (not used so leave 0 for off)
//  x       segment position G on (also Out 2)
//   x      segment position F on (also Out 1)
//    x     segment position E on (also Strike 2)
//     x    segment position D on (also Strike 1)
//      x   segment position C on (also Ball 3)
//       x  segment position B on (also Ball 2)
//        x segment position A on (also Ball 1)

// ---- animation modes ----
const int MODE_MANUAL = 0;
const int MODE_CHASE  = 1;
const int MODE_MULTI  = 2;
const int MODE_COUNT  = 3;

int testMode = MODE_MANUAL;        // current mode
unsigned long stepInterval = 500;  // ms between steps (changed via web UI)
unsigned long lastStepTime = 0;    // last time we advanced
int stepIndex = 0;                 // current position in the sequence

// Chase sequence: A, F, G, C, D, E, G, B
// Using the bit layout from num[] (LSB=A, then B,C,D,E,F,G)
const byte chaseSeq[] = {
  B00000001, // A
  B00100000, // F
  B01000000, // G
  B00000100, // C
  B00001000, // D
  B00010000, // E
  B01000000, // G again
  B00000010  // B
};
const int chaseLen = sizeof(chaseSeq) / sizeof(chaseSeq[0]);

// Multiples sequence: F+B, A+G, E+C, G+D
const byte multiSeq[] = {
  (B00100000 | B00000010), // F + B
  (B00000001 | B01000000), // A + G
  (B00010000 | B00000100), // E + C
  (B01000000 | B00001000)  // G + D
};
const int multiLen = sizeof(multiSeq) / sizeof(multiSeq[0]);


// store if new serial data should be sent to the HC595 shift registers or not
int flag_update = false;

// WiFi connection setup
byte mac[6];  // the MAC address of WiFi module

bool connectWiFi(const char* ssid, const char* pass, unsigned long timeoutMs) {
  WiFi.disconnect();
  delay(200);

  WiFi.begin(ssid, pass);

  unsigned long startAttemptTime = millis();

  while (WiFi.status() != WL_CONNECTED && millis() - startAttemptTime < timeoutMs) {
    delay(500);
  }

  return WiFi.status() == WL_CONNECTED;
}

int status = WL_IDLE_STATUS;
WiFiServer server(80);



void setup() {

  // set all the pins of 74HC595 as OUTPUT
  pinMode(latchPin, OUTPUT);
  pinMode(dataPin, OUTPUT);  
  pinMode(clockPin, OUTPUT);

  //Serial.begin(9600);      // initialize serial communication

  // check for the WiFi module:
  if (WiFi.status() == WL_NO_MODULE) {
    //Serial.println("Communication with WiFi module failed!");
    // don't continue
    while (true);
  }

  // check for the firmware upgrade:
  String fv = WiFi.firmwareVersion();
  if (fv < WIFI_FIRMWARE_LATEST_VERSION) {
    //Serial.println("Please upgrade the firmware");
  }

  // ---------- WIFI CONNECT WITH FALLBACK ----------
  bool connected = false;

  // try primary first
  connected = connectWiFi(ssid1, pass1, 12000);
  if (connected) {
    activeNet = 1;
  } else {
    // try fallback
    connected = connectWiFi(ssid2, pass2, 12000);
    if (connected) {
      activeNet = 2;
    }
  }

  // If neither worked, keep cycling forever (primary then fallback)
  while (!connected) {
    connected = connectWiFi(ssid1, pass1, 12000);
    if (connected) {
      activeNet = 1;
      break;
    }

    connected = connectWiFi(ssid2, pass2, 12000);
    if (connected) {
      activeNet = 2;
      break;
    }
  }


server.begin();     // start the web server on port 80

// ---------- WAIT FOR A REAL IP (not 0.0.0.0) ----------
IPAddress localIP;
unsigned long ipStart = millis();

// wait up to 10 seconds for DHCP
do {
  localIP = WiFi.localIP();
  if (localIP[0] != 0) break;   // got something real
  delay(200);
} while (millis() - ipStart < 10000);

// PRI or SEC depending on which network connected
String netLabel = (activeNet == 1) ? "PRI" : "SEC";

// If still no IP, we'll show 0.0 to make it obvious something's wrong
String label = netLabel + " ." + String(localIP[2]) + "." + String(localIP[3]);

matrix.begin();
matrix.beginDraw();
matrix.stroke(0xFFFFFFFF);
matrix.clear();
matrix.textFont(Font_4x6);
matrix.textScrollSpeed(80);   // adjust to taste

matrix.beginText(0, 1, 0xFFFFFF);
matrix.println(label);
matrix.endText(SCROLL_LEFT);
matrix.endDraw();


  flag_update = false;
}
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
